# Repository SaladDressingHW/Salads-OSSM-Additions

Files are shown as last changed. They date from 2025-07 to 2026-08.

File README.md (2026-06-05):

This repository has all of my additions, mods and revamps open for Download.
If you like my work, consider supporting me on [Ko-Fi](https://ko-fi.com/deepfantasies)!
# Permissions
You are welcome to edit/alter/remix, print and use the provided files freely. You are also encouraged to make additions and share them should you see the need for them. You may redistribute only your edits/remixes/alterations and additions with credits to this repo at least. If you want to print my files to sell them, ask me for permission per message first. 

All of the above applies to every project here.
# Capstan OSSM XL
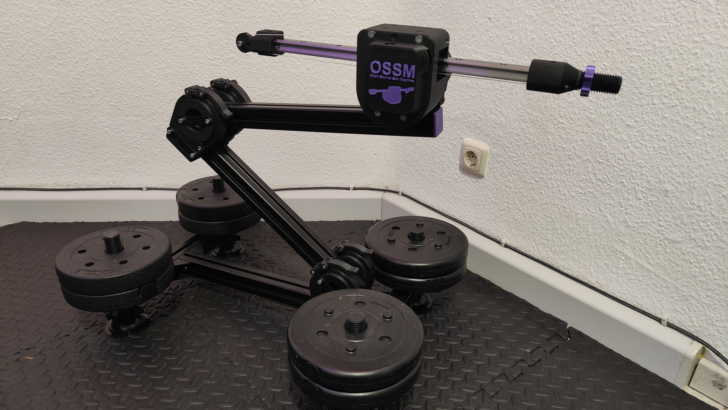
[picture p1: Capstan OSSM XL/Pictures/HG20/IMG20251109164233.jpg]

Revamp of the OSSM drive mechanism to use a capstan based version, enabling higher load use with a more powerful motor, namely the 60AIM40F.

Thread MGN12H: https://discord.com/channels/559409652425687041/1395456804464623817
Thread HG20: https://discord.com/channels/559409652425687041/1437149434143182959

# Capstan Proof of Concept
This was my first version. It is a proof of concept with quite a few flaws that I have abandoned to see if it is at all a viable concept. This is using 57AIM30 or 42AIM30 motors. You can try this first if you are sceptical to drop over a hundred bucks on a new motor. Bear in mind that quite a bit has changed since then. Changes that are not updated for this Proof of Concept. It worked good enough for me to use it, but it may not for you. The imo truly fleshed out Version is the Capstan XL.

Thread: https://discord.com/channels/559409652425687041/1331948206061256739

# 60AIM40F Motor Cover
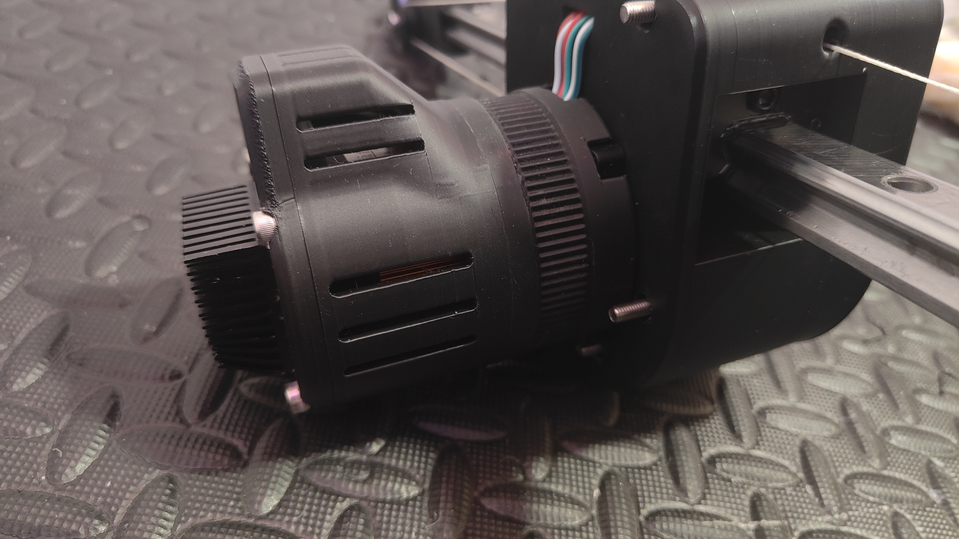
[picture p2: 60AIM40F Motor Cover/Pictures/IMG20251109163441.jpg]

Motor Cover for the 60AIM40F cover. Recommedned to only use with a heatsink attached to the back of the motor, where it gets really hot. Connects to armpits experimental 60AIM40F motor ring. For this, you need to replace the Nuts in the motor ring with M5x20 Coupling nuts. Then screw the Cover onto the motor with 4x M5x45 Hex Caps.

Thread: https://discord.com/channels/559409652425687041/1437144846510063636

# Double Penetration Attachment
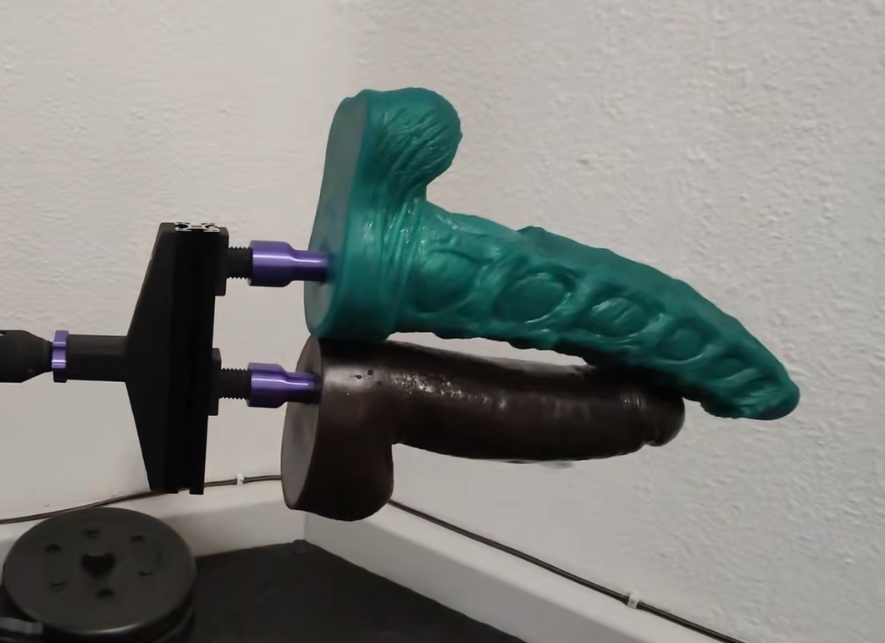
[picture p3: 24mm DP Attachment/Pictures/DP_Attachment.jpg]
DP_Attachment

A DP Attachment for 24mm threading. Uses a 200mm 3030 Aluminium Extrusion for extra stability and two on t-nuts slidable 24mm threads. Very heavy duty, very sturdy. Recommended to use with Capstan XL HG20 version but of course not required. Hardware needed are 4x M5x10 Hex Caps for the threads, 4x M5x20 for connecting the main part to the 3030 and 8 M5 T-Nuts.

Thread: https://discord.com/channels/559409652425687041/1437143419607847083

# Quick Change Strap Toy Mount remix

For compatibility with smaller print beds, I remixed @arctan and @marc_o_v [Quick Change Strap Toy Mount](https://discord.com/channels/559409652425687041/1278049440787337226). It detaches the straps from the Ring. From my experience, this is very secure and only slips under high load when lube come into contact with the connection. You need TPU filament.

Thread: https://discord.com/channels/559409652425687041/1279814763257397298

# Suction Cup Bracket

A bracket to mount [these](https://de.aliexpress.com/item/1005006355052746.html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) suction cups to 4040 extrusion (tested with aluxprofile Type I). The suction Cups are very strong, I use a total of 4 on my shicks mount. This has the big advantage to not loose any stability that comes with the shicks mount whatsover.
Requires one suction cup and one UNC-1/4 20 5/8" screw for each bracket.

Thread: https://discord.com/channels/559409652425687041/1395419104231559361

# Weight Plate Bracket

This is a bracket to mount standard 28-30mm inner diameter weight plates onto any extrusion. 2x M5x12 screws + 2x M5 T-Nuts required per Bracket 

Thread: https://discord.com/channels/559409652425687041/1279819188390596669

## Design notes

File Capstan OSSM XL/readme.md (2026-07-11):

Hundreds of hours of work as well as a lot of monetary resources go into this project! If you like my work, consider supporting me on [Ko-Fi](https://ko-fi.com/deepfantasies)!

# Capstan OSSM XL

Revamp of the OSSM drive mechanism to use a capstan based version, enabling higher load use with a more powerful motor, namely the 60AIM40F.

A Capstan Drive is based on rope and a pulley. For a nice video explaining the mechanism, check this awesome video by Aaed Musa: [https://www.youtube.com/watch?v=MwIBTbumd1Q](https://www.youtube.com/watch?v=MwIBTbumd1Q "https://www.youtube.com/watch?v=MwIBTbumd1Q")

**Why Capstan?**

The belt driven Version has shown for myself and quite a few others limitations. At higher torques, it would sometimes slip. Bear in mind, it could be that is the result from build or other errors.

**Comparison to the standard OSSM**

Pro:

 - same form factor
 - as quiet or quieter
 - 16.5cm rail length loss (e.g. 450mm rail -> 28.5cm stroke)
 - 2.7 times stronger (32kg compared to 12kg)
 - same speed
 - no slipping, reliable operation
 - PitClamp compatible
 - compatible with all custom end effectors

Con:

 - harder to build
 - bigger motor -> more expensive (~110€ shipped incl. tax to germany)
 - more to print
 - in extreme use cases there may be slipping of the rail over time, is fixed by rerunning homing
 - rope must always be tight -> regular checking
 - more heavy duty mounting recommended
 
The current iteration of the machine, that being the HG20 version, has been tested by me for many months now and has served all my needs. It also has been built and praised by many people in the KinkyMakers Discord Community.

Thread MGN12H: https://discord.com/channels/559409652425687041/1395456804464623817
Thread HG20: https://discord.com/channels/559409652425687041/1437149434143182959
# MGN12H vs HG20

**The MGN12H version is deprecated**

MGN12H rails and carriages get to their limit with 30cm+ cantilevers combined with heavy toys ~1.5kg and up. This results in louder operation, damaging of the bearings over time and deflection issues. So I recommend going with the HG20 Version if you plan to use big, heavy toys.
Additionally, the HG Version comes with a number of improvements such as a bigger drum and better rope guiding for even smoother operation.

I do consider the MGN12H version to be outdated so I do recommend going with HG20 if you can afford the +~40€ in cost.

# Rail Lengths
The Capstan Drum on the HG20 version was tested for 450mm. Shorter is always possible. 500mm and 550mm should be possible as well, but hasn't been tested by me (yet). Longer I do not recommend.

As for MGN12H, stay at 500mm or below.

# Rope
Use the rope I list (Liros DC pro 161). If you can't, try to source another dyneema dm20, sk99, sk75 max. diameter 1mm rope.

**DO NOT** use generic uhwmpe from aliexpress. Experiments from kind @neos have shown that the quality is shit. It stretches and breaks with load. It is essential that the rope stretches as little as possible. Lots of research has been done to find the correct rope. Stick to it. Or deviate at your own risk and cost.

# Printing
I have included .3mf file with configured settings. They require decent bridging performance. Some files don't have .3mf files. Those are quite straight forward to print. I always recommend 6 walls 20% infill.
# BOM
see /3D printed parts/MGN12H or /3D printed parts/HG20 respecively

Finally, special thanks to everyone that helped me and gave suggestions when I hit a wall!

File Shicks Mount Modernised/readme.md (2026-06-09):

# Shick's Mount Modernised
This is a modernisation, remix and compilation of the original Shick's Double Extrusion Mount as well as some mods done by [armpitMFG](https://github.com/armpitMFG). In addition to that, this is a centralized documentation for a heavy duty friendly mount, where even the biggest toys at long levers aren't able to make the mount slip. 

This is a WIP that is also still in testing, which is on hold due to lack of funds. Since it is just a reiteration (mostly making things bigger and stronger) of proven designs however, I am confident it will work nicely. I also have one more trick up my sleeve should the current strength still not suffice.

The Parts compiled and remixed here are the following:
| Part | Link | Modification(s) done |
|:---:|---|---|
| Original Double Extrusion Shicks mount | not hosted anywhere anymore, afaik | Just using the hinge long part + f3d files |
| 300° Hinge Plate by armpit | [Discord](https://discord.com/channels/559409652425687041/1214771415430078525) | Holes realligned, changed thickness |
| Lever Clamp System by armpit | [Discord](https://discord.com/channels/559409652425687041/1209004178421055598) | Reworked from the ground up to make it much bigger and more stable |
| Metal Hinge by Thomas & Me | [Discord](https://discord.com/channels/559409652425687041/1445780533991833810) | New Part |

# BOM
This BOM has heavy duty use in mind. Feel free to downscale for less demanding setups. More info in my beginners OSSM guide (releasing soon).
| Part | Amount | Link |
|:---:|---|---|
| 4040 Extrusion I recommend aluxprofile for people in Europe, Hinge is optimized for it (it's what I have on hand) | I use 2 x 400 mm for feet, 3 x 475 mm for arms | https://www.aluxprofil.de/aluminium-nutprofil-4040/a3619?m=4259 |
| 4040 end caps, or print your own | 8 for double arm | e.g. https://www.aluxprofil.de/profilabdeckkappe-4040/a3528 |
| 4080 corner brackets, best for heavy duty stability | 4 | https://de.aliexpress.com/item/1005009745995530.html |
| M8x80 adjustable lever | 1 per hinge | https://de.aliexpress.com/item/1005008368566274.html |
| Laser Cut Hinge Plates, stainless steel | 2 bottom (5mm) + 2 top (3mm) | "SideHingeLasered" files, order at your favorite laser cut shop, I use JLCCNC <br> [How to order from JLCCNC](https://github.com/SaladDressingHW/Salads-OSSM-Additions/blob/main/Salad's%20Beginner%20Guide%20to%20the%20'Ultimate'%20OSSM!/JLCCNC.md) |
| Hardware | see Hardware.txt | see Hardware.txt |

You will also need something to drill through the aluminium extrusion. A hand drill with according metal drill bit should suffice.

# Printing
**HingeLong**: You need 2 of these per Hinge. For 5mm hinge plates you will need the "Bottom" one, and for 3mm hinge plates the "Top" one. print them at an angle for best stability, see my .3mf. .3mf is for the Aluxprofile version as that is what I have. F3d file is attached so you can modify it to fit your own 4040 profile. Supports are needed. 6 Walls, 20% infill suffices.

**WasherBack**: Print one per hinge, again "Top" and "Bottom" versions depending on your plate thickness. Also needs to be printed at an angle, or it **will** break when tightening a lot. Again, see .3mf for orientation. Supports recommended. Print at 9 Walls or more to properly support the nut.

**WasherFront**: One is need per hinge. Print it 100% solid.

**TPU_Washer**: 2 per hinge are needed. Print it 100% solid. Out of TPU, as the name implies. I recommend printing TPU by Object for the least stringing. Especially if you haven't dried your Tpu like me.

# Assembly Guide
[Link](Assembly.md) (WIP)

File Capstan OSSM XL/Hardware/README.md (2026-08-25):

# BOM HG20

| Part | Cost (incl. shipping & tax) | link |
|---|---|---|
| 60AIM40F (+485 single turn version) | ~110€ | https://www.superbuy.com/en/page/buy/?url=https://item.taobao.com/item.htm?id=668578585661 <br><br> [How to order from Superbuy](https://github.com/SaladDressingHW/Salads-OSSM-Additions/blob/main/Salad's%20Beginner%20Guide%20to%20the%20'Ultimate'%20OSSM!/Superbuy.md) |
| RS485 to USB cable (for motor programming) | ~0€ | comes included with motor when bought from link above |
| OSSM Control Board + Remote (can buy board only if you want wireless remote) | 91 USD (excl. tax & shipping) | https://www.researchanddesire.com/products/ossm-reference-board |
| 2x 6 x 29.3 x 8 mm [id x od x w] U-Groove Pulley | ~8€ | https://de.aliexpress.com/item/1005007465275570.html |
| Hardware | ~30€ | see hardware/Hardware.txt |
| 1kg PLA | ~10€\kg | https://de.aliexpress.com/item/1005006639640810.html |
| 5m Liros DC pro 161 rope (or similar) | ~15€ | WW shipping: https://www.kitelineshop.com/ligne-liros-dcpro161-au-metre-c2x38222201  <br> US: https://www.mapleleafropes.com/store/category/new-england-ropes-hts-99-1 <br> Germany: https://www.blackbox-sailing.de/products/liros-dc-pro-kiteleine <br> EU: https://workshop.boardway.org/Liros-DC-Pro-161_1 |
| Bushing 20x24x40 (id x od x l) | ~5€ | https://de.aliexpress.com/item/1005009236377507.html |
| HG20 Linear Rail + HGH20HA Carriage | ~50€ (depending on length) | HG20 400/500mm + Carriage: https://de.aliexpress.com/item/4001272098866.html <br> HG20 other lengths: https://de.aliexpress.com/item/1005007417885303.html|
| Epoxy glue | ~3€ | https://de.aliexpress.com/item/1005007115129874.html |
| 4 pin JST PH2.0 header cable 30cm or solder/make your own | ~2€ | https://de.aliexpress.com/item/1005009087160808.html |
| 2 pin awg 18 or thicker 30cm | ~2€ | https://de.aliexpress.com/item/1005006614755156.html |
| 24mm id shrink tube | ~3€ | https://de.aliexpress.com/item/4000211463126.html |
| 36V 5+A power supply: Mean Well GST220A36-R7B + r7bf-p1j adaptor | ~68€ | GER: https://www.voelkner.de/products/2995507/MW-Mean-Well-GST220A36-R7B-Tischnetzteil-Festspannung-36-V-DC-6.1A-219.6W.html <br>**+**<br> https://www.voelkner.de/products/6716585/MW-Mean-Well-DC-PLUG-R7BF-P1J-Adapter.html <br> Look for your local distributors here: https://www.meanwell.com/distributors.aspx <br><br> Farnell, TME, Digikey and Rs-online ship to almost everywhere in the world! |
| **Total** | **~380€** | |

# BOM MGN12H [deprecated]

| Part | Cost (incl. shipping & tax) | link |
|---|---|---|
| 60AIM40F | ~110€ | https://www.superbuy.com/en/page/buy/?url=https://item.taobao.com/item.htm?id=668578585661 |
| OSSM Control Board + Remote (can buy board only if you want wireless remote) | 91 USD (excl. tax & shipping) | www.researchanddesire.com/products/ossm-reference-board |
| 5x MR115 bearings | ~3€ | https://de.aliexpress.com/item/1005007175995775.html |
| Hardware | ~30€ | see hardware/Hardware.txt |
| 1kg PLA | ~8€\kg | https://de.aliexpress.com/item/1005006639640810.html |
| 5m Liros DC pro 161 rope (or similar), ww shipping | ~15€ | https://www.kitelineshop.com/ligne-liros-dcpro161-au-metre-c2x38222201 |
| Bushing 20x23x30 (id x od x l) | ~5€ | https://www.agrolager.de/product_info.php?products_id=91534519 |
| MGN12H Linear Rail + Wagon | ~10-15€ (depending on length) | 450mm: https://de.aliexpress.com/item/1000007480470.html |
| Epoxy glue | ~3€ | https://de.aliexpress.com/item/1005007115129874.html |
| 4 pin JST header cable | ~2€ | https://de.aliexpress.com/item/1005007389108799.html |
| 2 pin awg 18 or thicker 30cm | ~2€ | https://de.aliexpress.com/item/1005006614755156.html |
| Kinesio Tape | ~3€ | buy locally (e.g. drug store) |
| 36V 5+A power supply (GST220A36-R7B + r7bf-p1j adapter) | ~68€ | https://www.voelkner.de/products/2995507/MW-Mean-Well-GST220A36-R7B-Tischnetzteil-Festspannung-36-V-DC-6.1A-219.6W.html <br>**+**<br> https://www.voelkner.de/products/6716585/MW-Mean-Well-DC-PLUG-R7BF-P1J-Adapter.html |
| **Total** | **~345€** | |

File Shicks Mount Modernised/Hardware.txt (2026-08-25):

- 16x M8x14 ISO7380 for 4x corner brackets
- 16x Sliding T-Nuts M8 for 4x corner brackets, check that it fits your extrusion! For Aluxprofile, take 3030 version: https://de.aliexpress.com/item/1005004658668930.html
- 6x M8x14 ISO7380 per Hinge
- 1x M8x60 Hex Cap per Hinge
- 3x M8x24 washer per Hinge
- 1x M8x40 washer per Hinge https://de.aliexpress.com/item/1005002399622506.html
- 6x sliding T-Nuts M8 per Hinge
- 2x M8 Nuts per Hinge

optional for GST220A36 power supply:
- 2x M5x20 Hex Cap
- 2x M8x20 Hex Cap
- 2x M5 Nut
- 2x M8 sliding T-Nut

Hex Cap: My designs are made for DIN 912/ISO 4762 Norm

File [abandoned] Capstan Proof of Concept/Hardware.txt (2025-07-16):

Hardware:

Tensioner:
 2x M3x30 Hex Cap
 4x M5x25 Hex Cap
 1x M5x50 Hex Cap
 
 2x M3 Nut
 5x M5 Nut

Motor Head:
 42AIM:
  2x M3x12 Countersunk
  6x M3x12 Hex Cap
  1x M4x16 Hex Cap
  5x M5x35 Countersunk

  5x M5 Nut
 
 57AIM30:
  1x M4x16 Hex Cap
  4x M5x30 Hex Cap
  2x M5x50 Hex Cap
  2x M5x80 Hex Cap
  
  4x M5 Nut

End Effector:
 2x M3x16 ISO7380
 2x M3 Nuts

Rope:
any of dyneema dm20, sk99, sk75 max 1mm diameter is a good option
I recommend, and the pulley is modeled for: liros dc pro 161 (sk99)
ww shipping shop: https://www.kitelineshop.com/ligne-liros-dcpro161-au-metre-c2x38222201

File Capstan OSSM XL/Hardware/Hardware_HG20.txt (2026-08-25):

2x M3x12 Hex Cap
4x M4x16 ISO7380
2x M5x45 Countersunk
4x M5x80 Countersunk
2x M6x25 Countersunk
4x M5x20 Hex Cap
3x M5x30 Hex Cap
4x M5x65 Hex Cap
1x M5x110 Hex Cap Fully threaded https://de.aliexpress.com/item/1005005879037174.html
11x M5 Nuts
4x M4 Nuts
2x M3 Nuts

Motor Cover:
4x M5x65 Hex Cap
4x M5x20 Coupling Nuts

Hex Cap: My Designs are made for DIN 912/ISO 4762 Norm

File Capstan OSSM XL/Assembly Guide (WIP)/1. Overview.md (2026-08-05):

# Welcome!
So you have decided on building a Capstan OSSM XL, or at least are thinking about it! It's always good to take a look before starting the process as well, so good on you! This doc is the first part of the Assembly Guide, and gives an Overview of the process. So let's get started!

<br>

## Step 1: Sourcing parts
This is probably the most unattractive part. This build has a lot of parts that you need. There are two ways that you can go about that!

#### The easy route:
 Head over to my [Etsy](https://www.etsy.com/shop/SaladsSexMachines) and order a Hardware Kit! Every item that you need to buy (except tools) is included there. Some items like the recommended rope can be hard to source in some parts of the world, so this might be a good option for you

#### The DIY route:
 Head over to the [BOM](https://github.com/SaladDressingHW/Salads-OSSM-Additions/tree/main/Capstan%20OSSM%20XL/Hardware) and source everything yourself! Quite a few things you will have to look for locally. More info in the following doc, [`Tools And Parts.md`](./2.%20Tools%20And%20Parts.md).

<br>

## Step 2: Print your parts
Again, you can do this two ways!

#### Printed Parts Kit:
3D printed part kits are ready to purchase, again from my [Etsy](https://www.etsy.com/shop/SaladsSexMachines). You can also message me to ask about personalizion options!

#### Print it yourself:
Head over to the [directory with the 3d printed parts](https://github.com/SaladDressingHW/Salads-OSSM-Additions/tree/main/Capstan%20OSSM%20XL/Hardware/3D%20printed%20parts/HG20). There are .stl and .3mf files both. The .3mf files include the settings and print orientations I use, and in some cases also painted supports. There are also .step files for all parts and in some cases .f3d as well so you can edit parts in case you want/need to modify something. More infos are provided in the following document, [`Tools And Parts.md`](./2.%20Tools%20And%20Parts.md). 
**Warning:** This project is **not** beginners friendly to print. You are expected to have some experience with 3D printing and a solid understanding of print settings and print optimization!

<br>

## Step 3: Prerequisites
There are still some other things that need to be done before assembly. Namely programming your Motor, flashing your PCB and glueing your Capstan Drum. Details and tutorials on how to do that are in the third document, [`Prerequisistes.md`](./3.%20Prerequisites.md).

<br>

## Step 4: Assembly
With everything sourced, printed and prepared, the machine can finally get assembled! This process is documented in the fourth and final document, [`Assembly.md`](./4.%20Assembly.md).

<br>

## Accessories and Mounting
You might be wondering what else you need. This guide is **only** for the Capstan OSSM XL, without any accessories or mounting. If you want or need guidance on the whole ecosystem, including mounting, modding and accessory options, check out my [Beginner's Guide](../../Beginner's%20Guide%20to%20the%20'Ultimate'%20OSSM!/)!

<br>

## Community
Finally, if you have any questions, problems, concerns, feedback or you just want to chat and share your OSSM (awesome) project, head over to the [Kinky makers Community over on discord](https://discord.gg/KVAGhvUkw)! We are a healthy community full of kinky makers and diyers happy to welcome anyone who is interested in it!

Happy building!

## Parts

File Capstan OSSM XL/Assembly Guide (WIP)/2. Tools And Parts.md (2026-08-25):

# Tools and Parts
This document gives and overview off all the parts, Hardware and Tools you need.

## 3D Printed Parts
These parts all need to be printed once! The files can be found [here](/../Hardware/3D%20printed%20parts/HG20/), both.stl and .3mf.
#### Print Settings:
Generally, the .3mf files contain the settings I print with, which are my recommended settings. However, each printer setup, print profiles and material is different, so please check and adjust settings and profiles accordingly. The .3mf files are optimized for eSun PLA Basic. In the following there are the core guidelines on what to pay attention to!
1. **Orientation:** Ignore the .stl orientations. Refer to the .3mf orientations instead. Do not reinvent the wheel. The orientations are crucial for the designs strength. The parts **will** break in the wrong orientation.
2. **Strength:** Most parts should be printed with at least 6 walls and 20% gyroid/cubic/similar infill. Adjust as needed depending on what material you print. Check the .3mf files to see which ones need less.
3. **Supports:** Due to the complexity of the design, many parts need supports. Please refer to the .3mf files for recommended support stucture. Some .3mf files have painted supports as well, for optimal printing.
4. **Layer Height:** Basically all prints are made for 0.2mm layer height and print well with it. The End Effector benefits strongly form adjsuting to 0.12mm or even 0.8mm layer height for a higher quality thread and overhangs. Many parts also benefit from variable layer height. Again, see the .3mf files to see if it is recommended on a part.
5. **Nozzle Size:** I have only ever printed with a 0.4mm nozzle, and therefore all my prints work well with that!
### Capstan Drum 
| Preview | File | Preview | File |
|---|---|---|---|
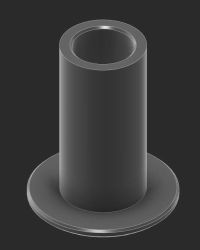
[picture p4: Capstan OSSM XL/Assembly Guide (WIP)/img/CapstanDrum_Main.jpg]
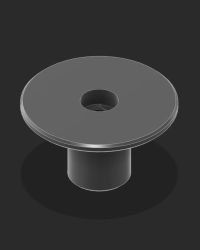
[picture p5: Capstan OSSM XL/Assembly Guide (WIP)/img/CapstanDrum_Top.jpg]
|  | `CapstanDrum_Main.stl` |  | `CapstanDrum_Top.stl` |

### Motor Head
| Preview | File | Preview | File |
|---|---|---|---|
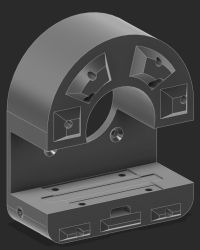
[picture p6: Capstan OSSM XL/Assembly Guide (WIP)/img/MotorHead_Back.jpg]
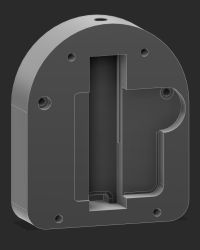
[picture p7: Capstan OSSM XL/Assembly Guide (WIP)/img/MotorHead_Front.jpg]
|  | `MotorHead_Back.stl` |  | `MotorHead_Front.stl` |
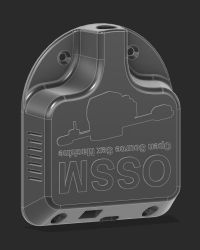
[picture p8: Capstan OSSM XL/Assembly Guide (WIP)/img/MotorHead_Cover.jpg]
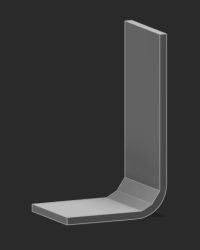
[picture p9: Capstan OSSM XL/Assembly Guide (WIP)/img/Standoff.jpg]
|  | `MotorHead_Cover.stl` |  | `Standoff.stl` |
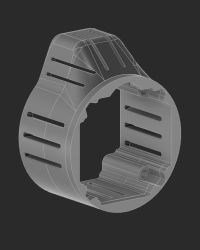
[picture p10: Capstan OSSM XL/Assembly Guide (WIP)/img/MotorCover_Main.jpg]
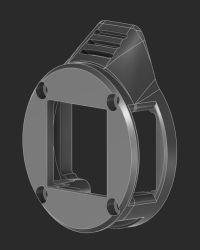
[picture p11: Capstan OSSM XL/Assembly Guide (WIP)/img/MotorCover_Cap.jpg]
|  | `MotorCover_Main.stl` |  | `MotorHead_Front.stl` |
|  | `Pitclamp_MotorRing_60AIM40F.stl` |  |  |

### EndEffector
| Preview | File | Preview | File |
|---|---|---|---|
|  | `EndEffector_<Hole End Offset>mm.stl` |  | `EndEffector_PulleyCover.stl` |

### Rail End
| Preview | File | Preview | File |
|---|---|---|---|
|  | `RailEnd_<Hole End Offset>mm.stl` |  | `RailEnd_PulleyCover.stl` |

### Tensioner
| Preview | File | Preview | File |
|---|---|---|---|
|  | `Tensioner_Bottom.stl` |  | `Tensioner_Top.stl` |

<br>

## Bill of Materials
The sourcing is mainly done for Gemrany, where I am based. Many linked parts ship worldwide or within Europe as well. You will need to look for your own sources, for your region if the provided sources don't work for you. Prices are rough estimates, with EU VAT, but without any additional costs attached (like the stupid new 3€/category from china imports).

**Rope:** The rope listed below can be quite hard to get depending on your region. There is a shop that claims worldwide whipping on the rope I develop the machine for, but users have reported theird orders getting canceled. You can still try it, it's still listed. I do not have the time and ressources to try lots of different ropes for every region. You have two options:
   1. Ask someone to ship it to you (Forwarding)
   2. Source a rope yourself and test it yourself. The important part here is that the rope is made out of Dyneema. Best case is Dyneema DM20, but Sk99 and SK78 work great as well. The Liros DC Pro 161 is made out of Dyneema Sk99. **Do not buy cheap aliexpress UHWMPE**. Testing has found that it is absolute crap that creeps ands stretches by unholy amounts. The second important part is that it is around 1mm in diameter, and this is where things get a bit harder most of the time. I wouldn't recommend going over 1.1-1.3mm. Thicker diameters may take away too much space on the drum, but feel free to test yourself. And if you do, pelase report!

| Part | Cost (incl. shipping & tax) | Link |
|---|---|---|
| 60AIM40F (+485 single turn version) | ~110€ | https://www.superbuy.com/en/page/buy/?url=https://item.taobao.com/item.htm?id=668578585661 <br><br> [How to order from Superbuy](https://github.com/SaladDressingHW/Salads-OSSM-Additions/blob/main/Salad's%20Beginner%20Guide%20to%20the%20'Ultimate'%20OSSM!/Superbuy.md)|
| RS485 to USB cable (for motor programming) | ~0€ | comes included with motor when bought from link above |
| OSSM Control Board + Remote (can buy board only if you want wireless remote) | 91 USD (excl. tax & shipping) | https://www.researchanddesire.com/products/ossm-reference-board |
| 2x 6 x 29.3 x 8 mm [id x od x w] U-Groove Pulley | ~8€ | https://de.aliexpress.com/item/1005007465275570.html |
| Fasteners & Nuts | ~30€ | see section below |
| 1kg PLA | ~10€\kg | use whatever works for you |
| 10m Dyneema DM20/SK99/SK78 Rope <br> Standard: Liros DC Pro 161 <br> NA: New England Ropes HTS 99 | ~15€ | WW shipping: https://www.kitelineshop.com/ligne-liros-dcpro161-au-metre-c2x38222201  <br> US: https://www.mapleleafropes.com/store/category/new-england-ropes-hts-99-1 <br> Germany & EU: https://www.blackbox-sailing.de/products/liros-dc-pro-kiteleine <br> EU: https://workshop.boardway.org/Liros-DC-Pro-161_1 |
| Bushing 20x24x40 (id x od x l) | ~5€ | https://de.aliexpress.com/item/1005009236377507.html |
| HG20 Linear Rail + HGH20HA Carriage | ~40€ (depending on length) | HG20 400/500mm + Carriage: https://de.aliexpress.com/item/4001272098866.html <br> HG20 other lengths: https://de.aliexpress.com/item/1005007417885303.html |
| Epoxy glue | ~3€ | https://de.aliexpress.com/item/1005007115129874.html |
| 4 pin JST PH2.0 header cable 30cm | ~3€ | https://de.aliexpress.com/item/1005009087160808.html |
| 2 pin awg 18 or thicker 30cm | ~2€ | https://de.aliexpress.com/item/1005006614755156.html |
| 24mm id shrink tube | ~4€ | https://de.aliexpress.com/item/4000211463126.html |
| Heat Sink 40x40x20mm | ~7€ | https://de.aliexpress.com/item/1005007090772998.html |
| 36V 5+A power supply: Mean Well GST220A36-R7B + r7bf-p1j adaptor | ~68€ | GER: https://www.voelkner.de/products/2995507/MW-Mean-Well-GST220A36-R7B-Tischnetzteil-Festspannung-36-V-DC-6.1A-219.6W.html <br>**+**<br> https://www.voelkner.de/products/6716585/MW-Mean-Well-DC-PLUG-R7BF-P1J-Adapter.html <br> Look for your local distributors here: https://www.meanwell.com/distributors.aspx <br><br> Farnell, TME, Digikey and Rs-online ship to almost everywhere in the world! |
| Isopropyl Alcohol || local Hardware Store |
| **Total** | **~390€** | |

<br>

## Fasteners & Nuts
The table below lists all the dasteners and nuts you need and what it is used for.

| Screw  | Type | Amount | Usage |
|---|---|---|---|
| M4x16  | Button Head | 4 | Tensioner Rope Clamp |
| M5x45  | Countersunk | 2 | Attaching Motor Head Back to Motor |
| M5x80  | Countersunk | 4 | Attaching Motor Head Cover to Motor Head |
| M6x25  | Countersunk | 2 | Mounting U-Groove Pulley to End Effector and Rail End |
| M3x12  | Hex Cap | 2 | Attaching the PCB to the Motor Head Cover |
| M5x20  | Hex Cap | 4 | Mounting HGH20HA Carriage to Motor Head Back |
| M5x30  | Hex Cap | 3 | 2x: Mounting End Effector and Rail End to HG20 Rail <br> 1x: Securing Capstan Drum to Motor shaft |
| M5x65  | Hex Cap | 8 | 2x: Attaching Motor Head Back to Motor <br> 2x: Attaching Motor Head Front to Motor Head Back <br> 4x: Mounting Motor Cover to Motor Head |
| M5x110 | Hex Cap, [fully threaded](https://de.aliexpress.com/item/1005005879037174.html) | 1 | Rope Tensioner Screw |
| M3 | Nuts | 2 | Attaching the PCB to the Motor Head Cover |
| M4 | Nuts | 4 | Rope Tensioner Clamp |
| M5 | Nuts | 9 | 6x: Back of Motor Head Back <br> 2x: End Effector and Rail End <br> 1x: Rope Tensioner Clamp |
| M6 | Nuts | 2 | End Effector and Rail End |
| M5x20  | Coupling Nuts | 4 | Coupling Motor Head to Motor Cover |

#### Standards:
- Button Head Screws: ISO 7380
- Countersunk Screws: ISO 10642
- Hex Cap: ISO 4762, except fully threaded M5x110
- Nuts: DIN 934, ISO 4033 should work

## Tools
You don't need much at all to build this machine! Very basic tools:
1. Screwdriver
2. Hex Bits sizes 2.5mm, 3mm & 4mm. I use this bitset: https://de.aliexpress.com/item/1005006233315642.html
3. Slotted Bit 2mm
4. Pliers
5. lint free cloth (e.g. glasses cleaning cloth)
6. household single use gloves
7. Heatgun/Hairdryer/Lighter

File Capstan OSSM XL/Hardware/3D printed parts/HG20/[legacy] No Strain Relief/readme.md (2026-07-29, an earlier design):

### Only use this version if you do not have or can buy the recommended Power Supply, Mean Well GST220A36.R7B + Adapter. This version is now considered legacy. I strongly recommend making the version with integrated Strain Relief!
hardware is the same as the version with strain relief!

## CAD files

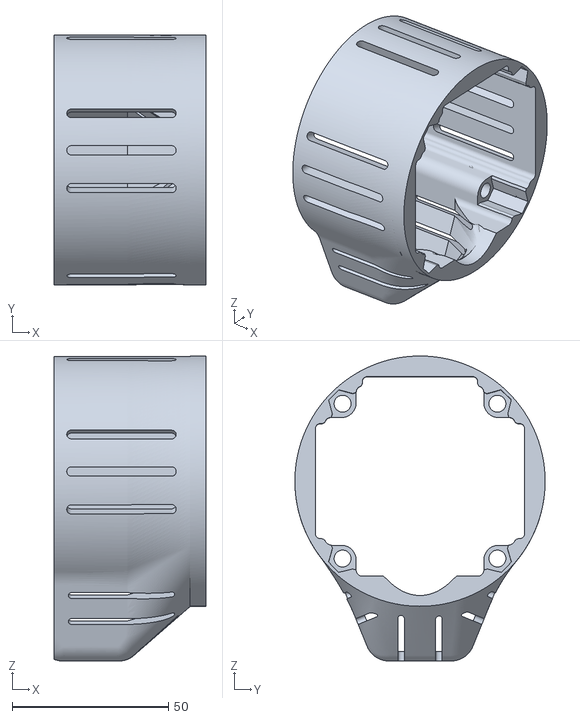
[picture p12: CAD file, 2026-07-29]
Capstan OSSM XL/Hardware/3D printed parts/HG20/MotorCover_Main.stl
48.4 x 80.0 x 97.5

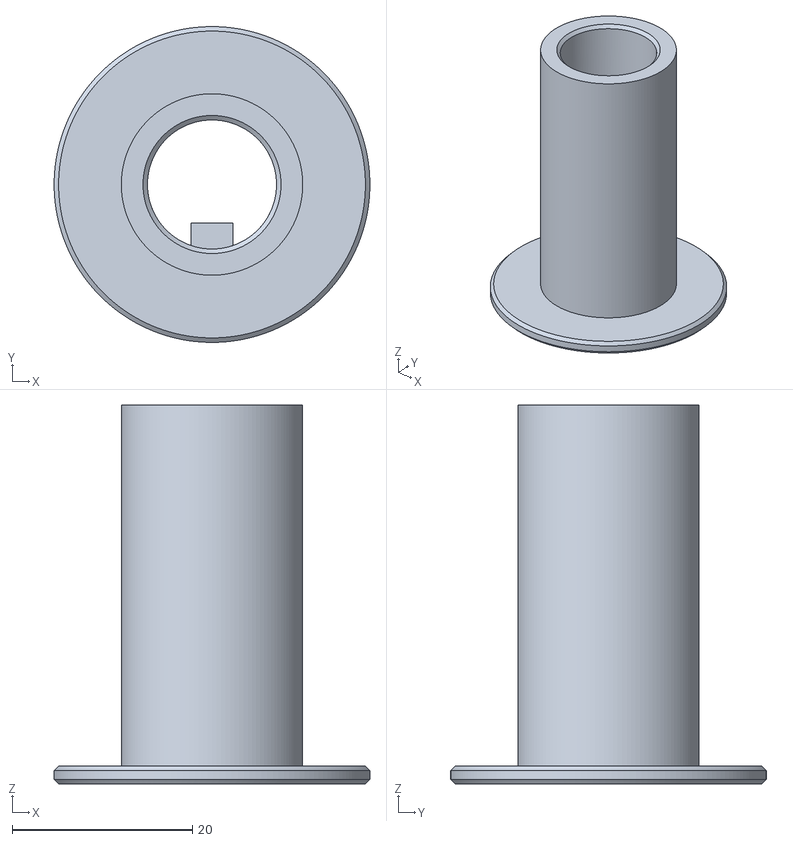
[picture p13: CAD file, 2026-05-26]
Capstan OSSM XL/Hardware/3D printed parts/HG20/CapstanDrum_Main.stl
35.0 x 35.0 x 42.0

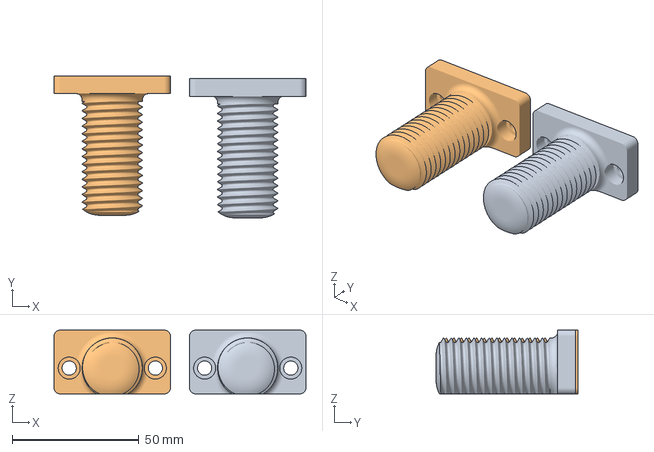
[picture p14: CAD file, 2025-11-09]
24mm DP Attachment/DP_Attachment_Thread.3mf
99.4 x 56.0 x 25.2 mm
DP_Attachment_Thread.stl x 2

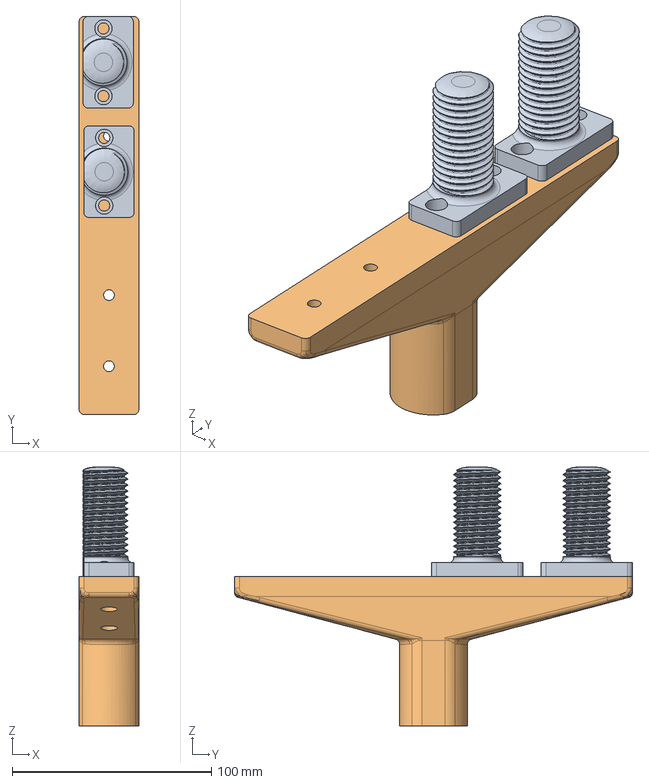
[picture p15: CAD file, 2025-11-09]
24mm DP Attachment/STEP/DP_Attachment.step
30.0 x 200.0 x 130.0 mm

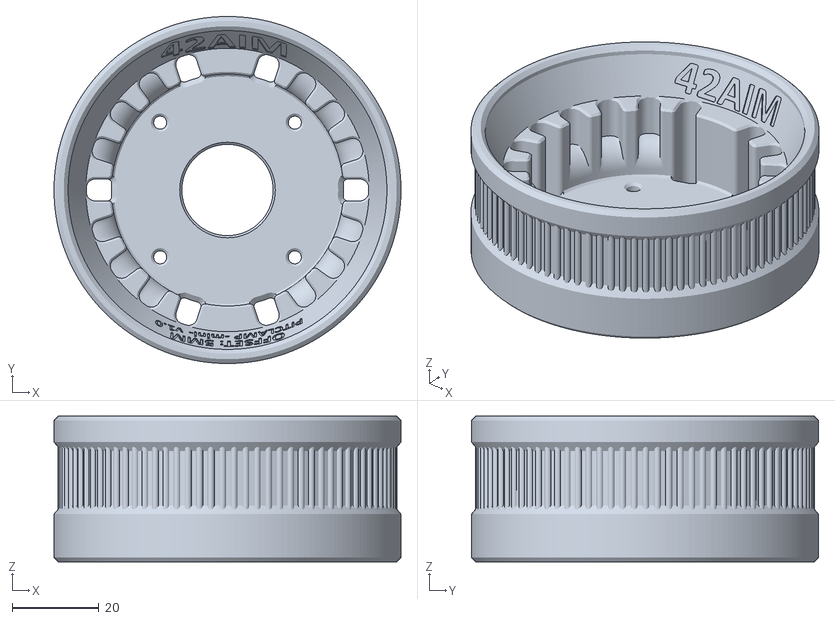
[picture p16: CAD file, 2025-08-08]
[abandoned] Capstan Proof of Concept/42AIM30/PitClamp Mini - Ring - 42AIM - Centered - 5mm Offset.stl
79.9 x 79.9 x 33.5

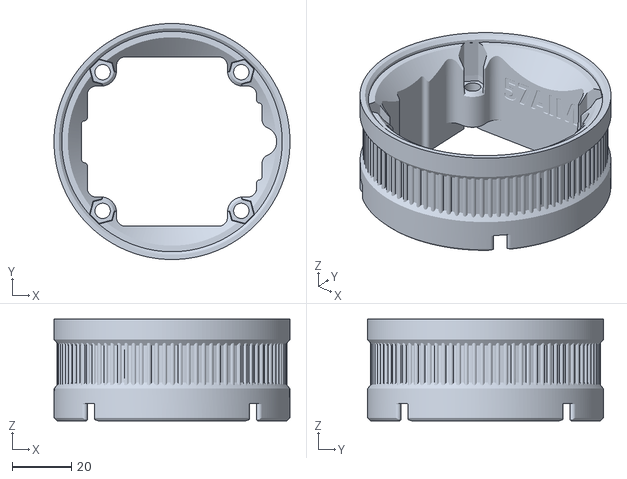
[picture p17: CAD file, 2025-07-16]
[abandoned] Capstan Proof of Concept/57AIM30/PitClamp Mini - Ring v1.1 - 57AIM - 5mm Offset +Passthru.stl
80.0 x 80.0 x 34.5

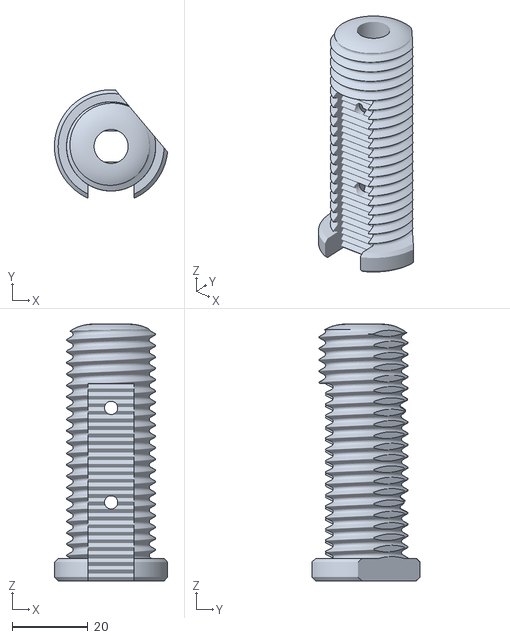
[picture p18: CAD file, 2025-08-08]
[abandoned] Capstan Proof of Concept/End Effector/End Effector.stl
29.9 x 28.7 x 68.0

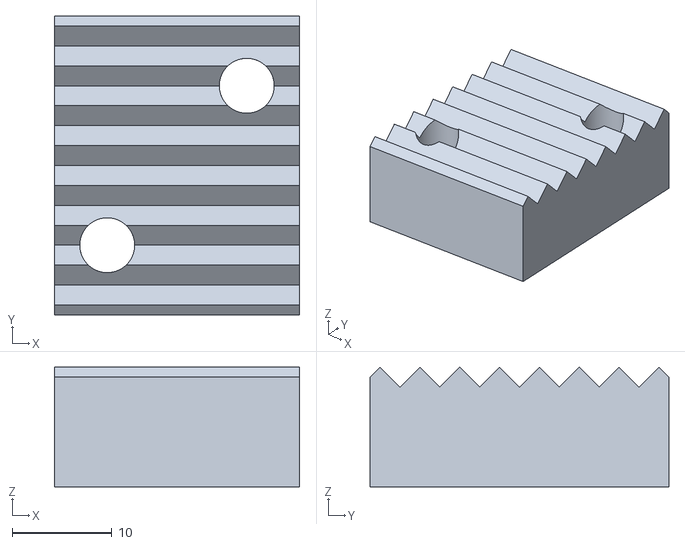
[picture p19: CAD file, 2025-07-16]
[abandoned] Capstan Proof of Concept/Tensioner/RopeClampUpper.stl
24.6 x 30.0 x 12.0

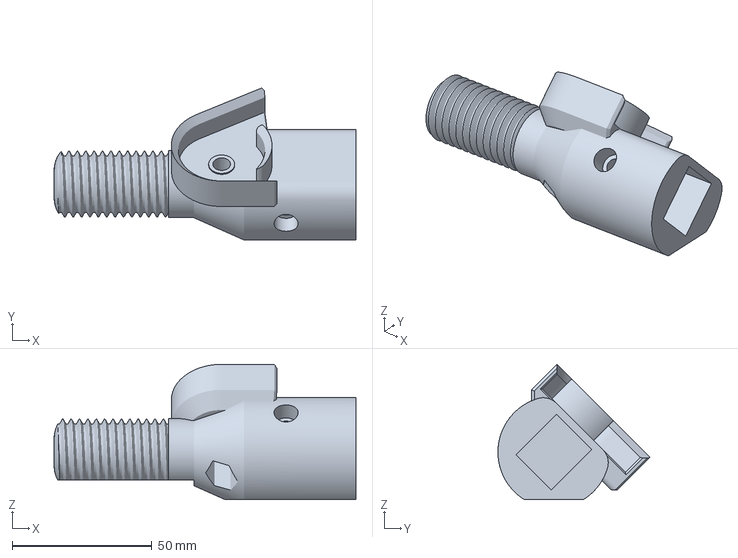
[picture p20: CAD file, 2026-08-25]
Capstan OSSM XL/Hardware/3D printed parts/HG20/EndEffector_15mm.3mf
108.0 x 54.4 x 48.4 mm

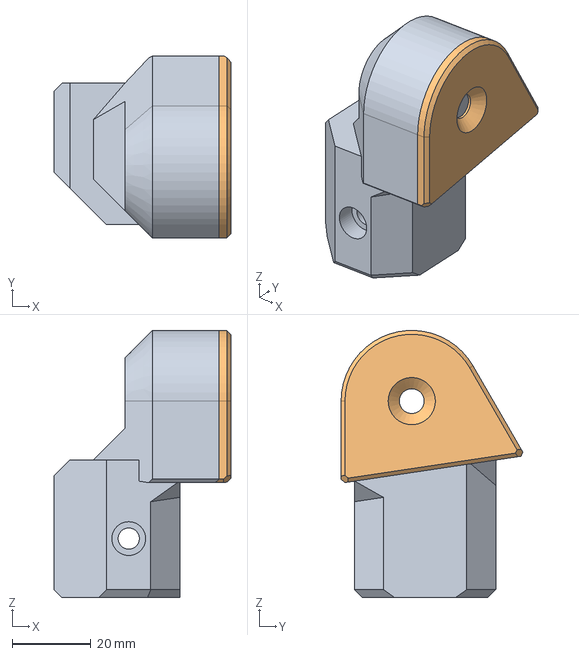
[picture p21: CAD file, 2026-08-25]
Capstan OSSM XL/Hardware/3D printed parts/HG20/STEP/RailEnd.step
45.0 x 46.3 x 68.0 mm

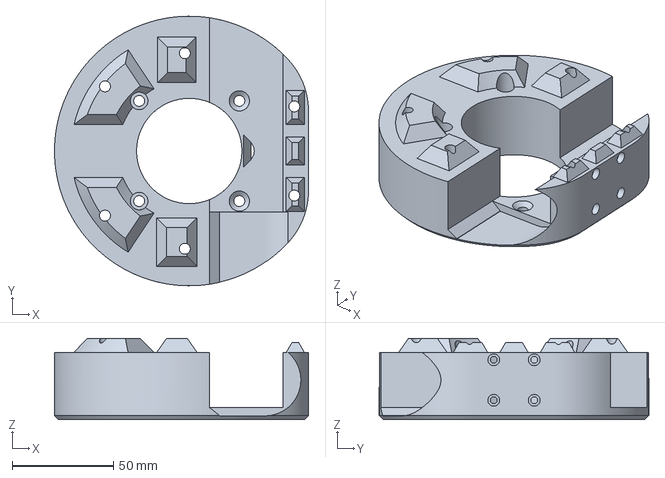
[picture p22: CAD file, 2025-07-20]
Capstan OSSM XL/Hardware/3D printed parts/MGN12H/AIO Mod/MotorHead_BackAIO.3mf
125.5 x 133.1 x 40.2 mm

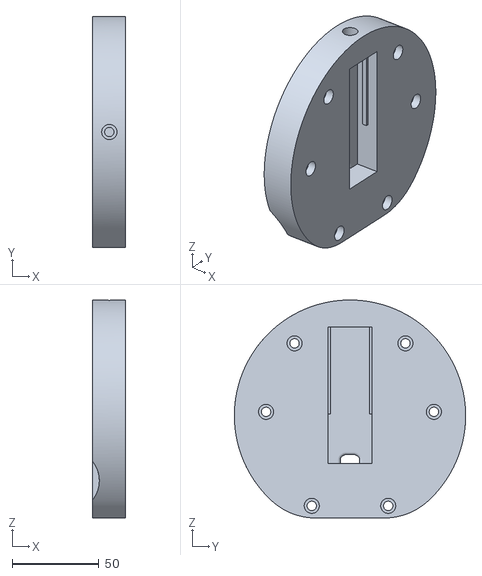
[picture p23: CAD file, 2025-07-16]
Capstan OSSM XL/Hardware/3D printed parts/MGN12H/Normal/MotorHeadFront.stl
19.1 x 133.1 x 125.5

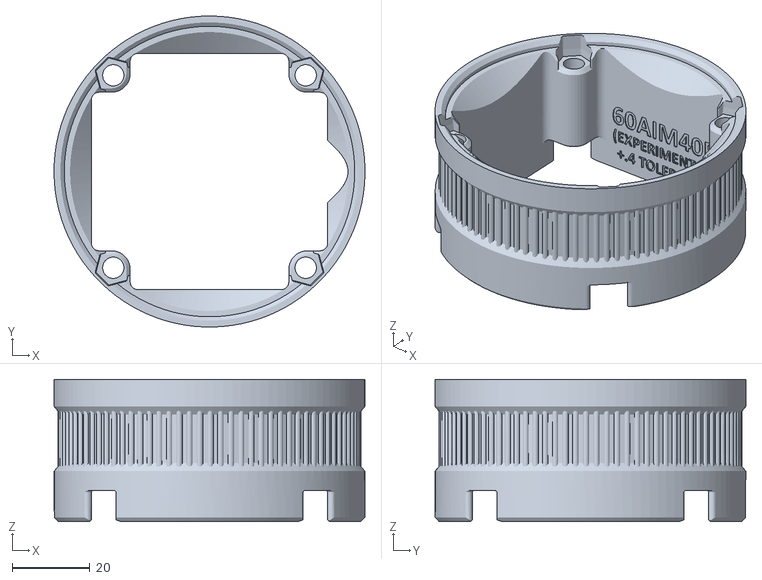
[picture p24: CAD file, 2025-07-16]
Capstan OSSM XL/Hardware/3D printed parts/MGN12H/PitClamp Mini - Ring - 60AIM40F - 7mm Offset + Bigger Passthru - by @armpit.stl
80.0 x 80.0 x 36.5

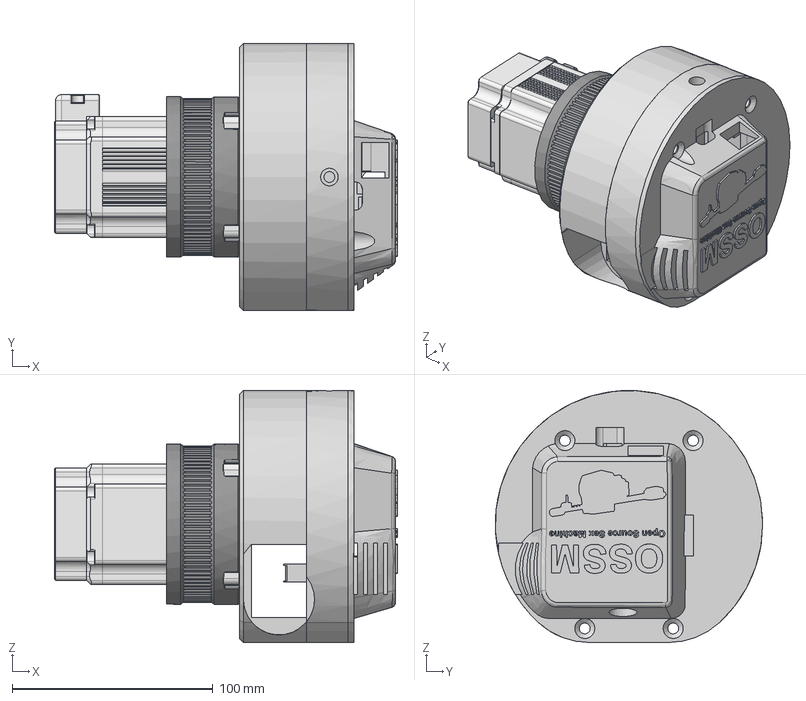
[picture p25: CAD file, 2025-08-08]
Capstan OSSM XL/Hardware/3D printed parts/MGN12H/STEP/MotorHead_60AIM40F.step
170.7 x 133.1 x 125.5 mm
6040方电机_简化_1
Graphic
60AIM40F Ring

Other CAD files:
Quick Change Strap Toy Mount Remix/Ring40mm.stl
Shicks Mount Modernised/SideHingeLasered_Bottom.step
Suction Cup Bracket/SuctionCupBracket - 3030 Amazon by neos.step
[abandoned] Capstan Proof of Concept/End Effector/End Effector Upper.stl
24mm DP Attachment/DP_Attachment.3mf
24mm DP Attachment/DP_Attachment.stl
24mm DP Attachment/DP_Attachment_Thread.stl
Capstan OSSM XL/Hardware/3D printed parts/HG20/CapstanDrum.3mf
Capstan OSSM XL/Hardware/3D printed parts/HG20/CapstanDrum_HGR.f3d
Capstan OSSM XL/Hardware/3D printed parts/HG20/CapstanDrum_Top.stl
Capstan OSSM XL/Hardware/3D printed parts/HG20/EndEffector_10mm.3mf
Capstan OSSM XL/Hardware/3D printed parts/HG20/EndEffector_10mm.stl
Capstan OSSM XL/Hardware/3D printed parts/HG20/EndEffector_15mm.stl
Capstan OSSM XL/Hardware/3D printed parts/HG20/EndEffector_20mm.3mf
Capstan OSSM XL/Hardware/3D printed parts/HG20/EndEffector_20mm.stl
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

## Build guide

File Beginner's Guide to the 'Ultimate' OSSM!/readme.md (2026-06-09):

**WIP**

# Welcome!
Are you **sick and tired** of **underwhelming** machines that are just copy pastes of each other? **Annoying** stroke depth adjustment by changing fly wheel radius? The same sinusoidal back and forth movement with **no pattern control**? **Underwhelming force** that **stalls** at anything bigger than a **toothpick**?
Ohhh do I have a solution for you! :DD

All tongue in cheek aside, that solution is called the **OSSM**, pronounced "awesome" and short for "Open Source Sex Machine"! As the name implies, it is an open souirce sex machine project, hosted on the official OSSM Github [here](https://github.com/KinkyMakers/OSSM-hardware/tree/main), with it's development and community based on the KinkyMakers Discord (I know, Discord for developing, bleh) [here](https://discord.gg/NcueGt87u).
The main features that sets it apart from other machines is real time adjustable stroke length and depth, pattern control with a big selection as well as documentation how to make your own, compactness, and strength. And all this at a relatively low price. It is 3d printed, and relatively easy and beginner friendly to assemble with great documentation. All other parts are of the shelf components you can easily get at places like aliexpress or amazon. Pick your poison :) I recommend checking out the repository for more information on the project.

## Do I need an alternative design?

Now while the machine is already quite powerful as is, with a pushing force of 12kgf (meaning it can push 12kg), it may not prove to be enough force for many users that, like myself, like to use **BIG** toys. From my and many other users experience, the standard build of the OSSM tends to stall with larger toys. Where that point is, is different from person to person. For some, it happens at sizes like large bad dragon toys, for others that is already the case with medium sized toys, especially knotted ones. That stalling is even more so the case for people with strong pelvic floors, especially if they cramp a lot during stimulation. This reasoning applies to both vaginal and anal use, although anal generally requires more force than vaginal use.

If you want to test out how much force you need, a hacky but simple way of doing that is taking the biggest toy that you want to use with it, place it on a scale and sit down on it. Put on all the force you can and try to push the toy out a bit for good measure. Add a few kg of redundancy to the biggest value you see on the scale, and you have your required force.
If that value is below 12kg, you are probably good to go with the standard design! But I do recommend to keep reading, there are a two other things to consider as well!

<br>

The first thing to consider is toy weight! The standard design uses a MGN12H linear rail. It's definitely a very great and capable rail that works for most toys, but the longer the rail length and therefor possible stroke depth, the higher the load will be on the bearing, that being the carriage block. This goes along with weight of toys. So, if you use bigger toys, that are also heavier and require longer stroke length to use the whole length on the machine, you multiply the load on the rail mounting. The force gets so high, that it can damage the rail over time and/or make it very loud.
So, the logical conclusion, at least mine, is to throw a bigger, beefier rail at it!

Now what you essentially need to check is the weight of your toys! The rail length you will choose does matter here, but as a general rule of thumb I recommend skipping on the standard design if you want to use toys heavier than 1.5kg!

<br>

The second thing that may influence your decision, is your expected "progress". Do you expect to size up over time? How much do you expect to size up? Will that push you over the edge where you might need a stronger machine? This is worth thinking a bit about, or you might have to upgrade at some point, which means you essentially spend the same money twice.

## So what is the alternative?
For the above described personal gripes I have with the standard design, I developed my own machine. That machine is called the **Capstan OSSM XL**, or **Capstan XL**. It completely revamps the Hardware to enable use of a motor ~twice as powerful as the original one, giving you a total of 32kgf pushing force! By this point it has been tried and tested by many users, and the feedback incorporated into multiple updates and iterations, to this day.

## What *exactly* is the Capstan XL?

For this question, I will kindly refer you to my readme over here: https://github.com/SaladDressingHW/Salads-OSSM-Additions/blob/main/Capstan%20OSSM%20XL/readme.md

## Do I need one?
Well that is for you to deecide of course! But in my opinion, if you fall out of the  (in my opinion) restrictions of the standard design, I don't see a reason to not go with the Capstan XL! If you do have any questions or are unsure, feel free to hop on the discord and ask away! other methods of getting in contact with me are gonna get established in the future!

## Okay I have decided!
Great! If you have decided for the standard build, just head over to the main repo and follow the instructions there!
If you have decided for the Capstan XL instead, you have multiple options>
   1. DIY all the way! <br>
    The [Capstan XL repository](https://github.com/SaladDressingHW/Salads-OSSM-Additions/tree/main/Capstan%20OSSM%20XL) has clear instructions on how you can build your own machine! Start by reading through it, take a look at the readme, BOM and Assembly instructions! Bear in mind that this is definitely not the best project for beginners! The 3D prints are more difficult and the assembly is definitely more involved and difficult than the standard build. That being said, I put a lot of effort in making it as accessible as possible with the time I have on my hands!
   2. Assemble yourself Kits <br>
    If you don't want to go through the pain (do some people actually like it?) of sourcing aaall the different parts, 3D printing every part and making sure everything fits as well 3D printing everything yourself, you can get DIY kits in different variations on my Etsy page! This also supports me and the continuous development of the machine!
   3. Buy assembled! <br>
      If you don't want to bother with neither sourcing nor a bit finicky assembly, you can buy assembled Capstan XL on the same Etsy page. As with the option before, this als odirectly supports me and the development of this and other projects!

Bear in mind that my Etsy currently only serves continental Europe!

## What else do I need?
There are quite a lot more things you need for a fully functioning machine. Because that is so much, I have divided this guide up into multiple parts. Click on the links below to get to the documents. This also serves as an overview.

1. **Mounting**:<br>You need to attach the machine somehow to something that makes it able to hold the machine in place, whereever you want. For this, there are quite a few Mounting options. See more in the dedicated file.
2. **Toy Attachments**:<br> No matter the version, the OSSM comes with a 24mm thread at the front, the so called "End Effector". This is a universal standard where all different Mounting and attachment systems for toys get screwed onto!
3. **Remote**:<br> Well, you need something to actually control the machine, right?
4. **Accessories**:<br> More optional parts that can be nice to have, depending on your preferences and use case!

## That's it!
This and the documents linked above should give you an guide you through everything you need! Bear in mind that I am not able to cover everything, because there is jsut too much! Additionally, there is new stuff being released quite regularily. So if you are not quite happy with what I list, always feel free to hop onto the discord and check out all the amazing stuff in #ossm-print-testing and #member-projects!

And last but not least: 

**Have fun!**

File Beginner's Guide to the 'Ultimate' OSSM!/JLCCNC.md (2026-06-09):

This short guide covers on how to order laser cut designs at JLCCNC, e.g. for the hinge for the [Shick's Mount Modernised]()!
1. Go to [JLCCNC's Website](https://jlccnc.com/)
2. Click on the big blue button "Get Isntant Quote" or in the top right "Order Now"
3. In the top row labeled "Select Product", scroll to the right and select "Sheet Metal"
4. Now upload the .step models provided in the repo by dropping them into the according field.
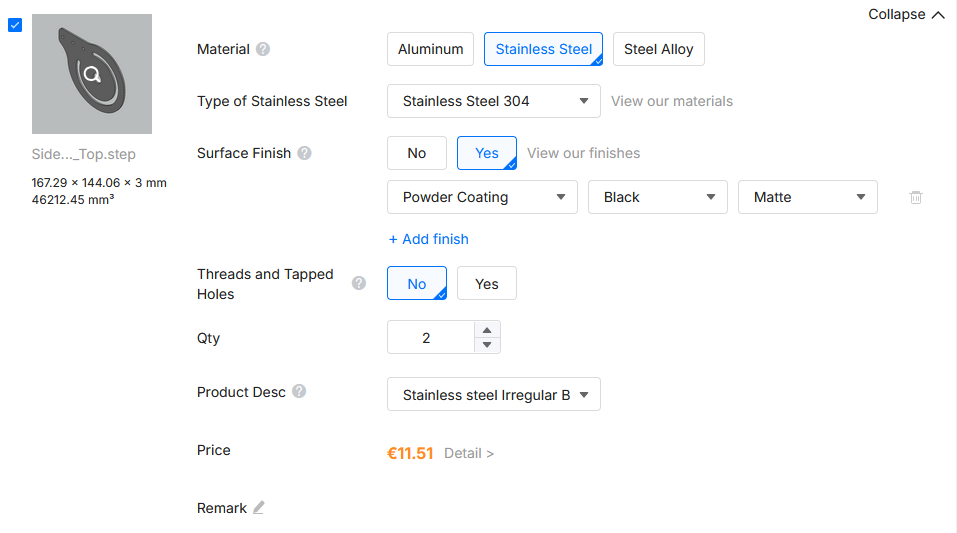
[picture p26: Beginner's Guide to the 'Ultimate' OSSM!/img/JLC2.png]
5. Select these settings: <br>
   You can choose any surface finish you like, or none at all, according to your preference!
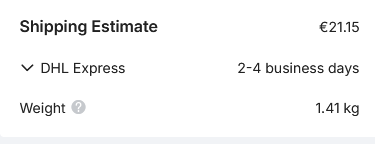
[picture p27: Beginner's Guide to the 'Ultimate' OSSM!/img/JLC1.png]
6. In the order summary on the right, look at the shipping. Open the shipping selection menu by clicking on the drop down arrow:<br> 
   Select the shipping according to your preferences. I usually go with EuroPacket, it's cheap.
7. Now press "Order"! Unfortunately you will need to create an account.
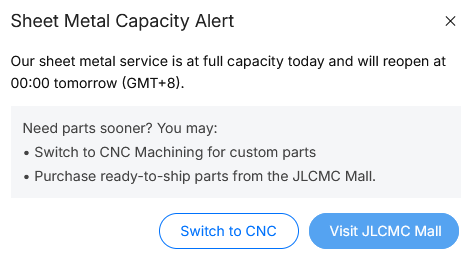
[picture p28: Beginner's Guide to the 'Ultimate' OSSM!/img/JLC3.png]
8. You may get a popup like this:<br> 
   Just come back at the stated time, in this case "tomorrow 00:00 GMT+8" and try to order again. Be on time for the best chances to get your order out. You may need a couple tries.
9. That's all! Enjoy!

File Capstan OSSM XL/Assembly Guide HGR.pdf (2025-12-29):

1. Bushing Pulley/Spindle/Drum/Capstan:
1. With the Bushing Pulley files printed, make sure the Bushing/Bearing Shell fits on top of the drum. Shouldn't be too loose or too tight. Top Part needs to fit on top as well with a somewhat secure fit. Also assure the pulley fits onto the motor shaft. Shouldn’t be too tight or loose. If things don't fit, adjust with the included .f3d file or pm me.
2. Take the bushing and slide the 24 mm shrink tubing on top. Cut it off so it fits well.
3. Heat the shrink tubing with a lighter or a heat gun. You can hold the bushing with some tongs or pliers, so you don’t burn yourself. Make sure to heat everywhere so it sticks to the bushing properly.
4. Spread some epoxy 2 part glue on the Bottom printed file.
5. Slide the Bushing/Bearing Shell on top. Put on the top part as well.
6. Put some weight on the Pulley and let it dry for 24h under pressure
7. Make sure the bushing holds well. It should be very rigid.

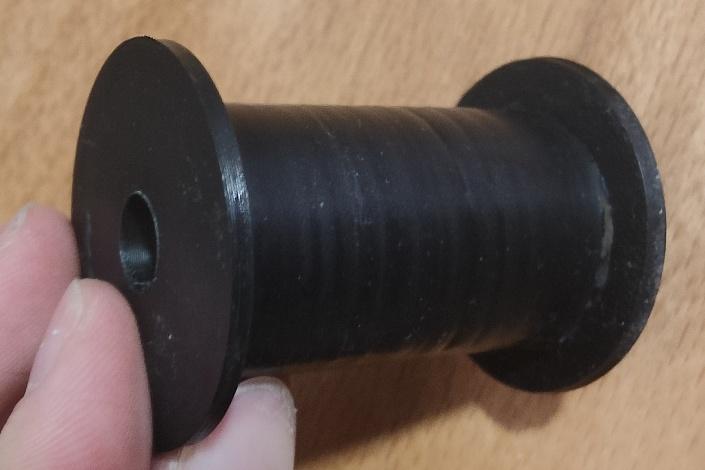
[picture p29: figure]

2. Clean the HGR20 Rail and HGH20HA Carriage (e.g. soaking in 99% isopropyl alcohol). Lube the carriage up well before mounting with some silicone grease

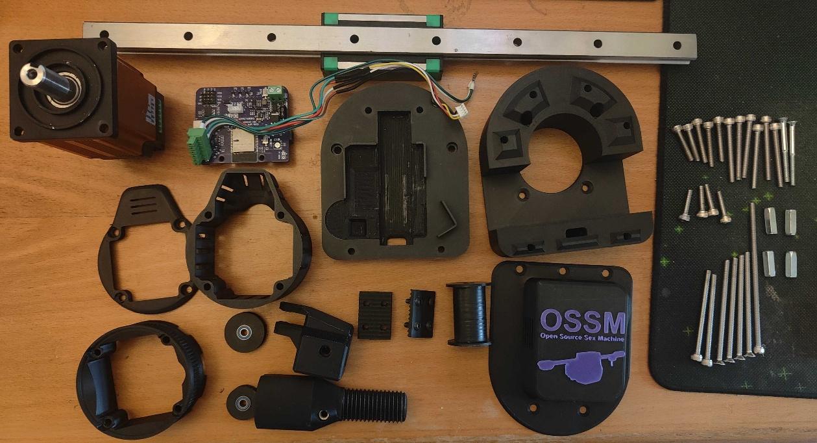
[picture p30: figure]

3. Mount the Motor Head Back to the Motor with Armpit’s 60AIM40F Ring behind (optional, if you want PitClamp Mounting) with 2 Hex Cap M5x65, 2 Countersunk M5x45 Screws and 4 M5 Nuts on the back. If you want to use the Motor Cover (https://github.com/SaladDressingHW/Salads-OSSM-Additions/tree/main/60AIM40F%20Motor%20Cover) replace the Nuts with M5x20 Coupling Nuts (as pictured). Make sure the Motor Terminal and the Notch in the Motor Ring are aligned to each other and the cable hole in the Motor Head Back right below the motor shaft. Ignore the cable in the second picture.

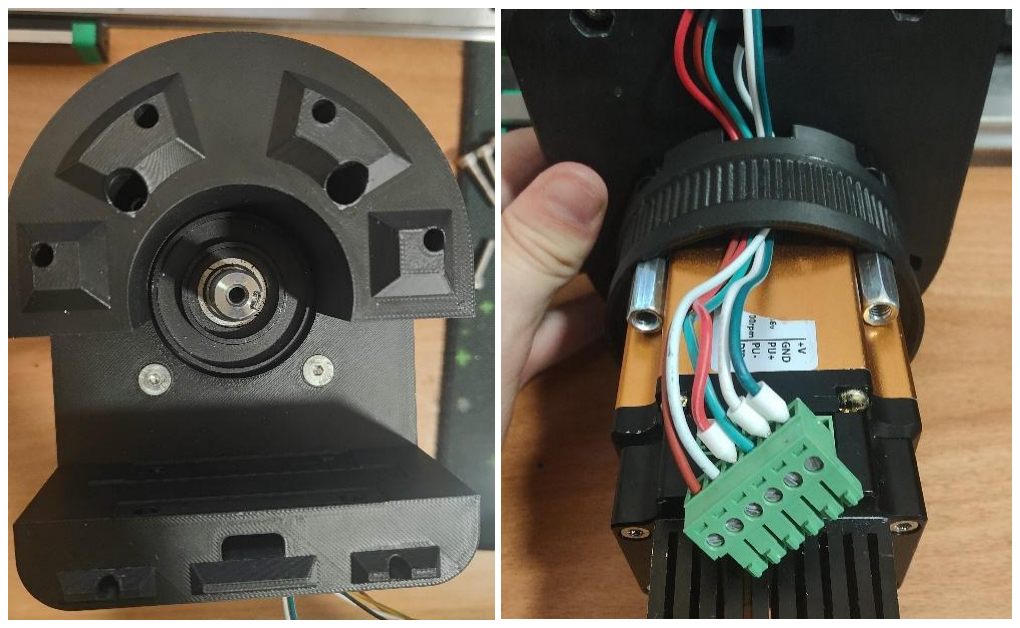
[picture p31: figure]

1. Screw the HGH20HA Rail Carriage to the Motor Head Back with 4 Hex Cap M5x20 screws. Slide the rail onto the carriage with the help of the plastic guide.

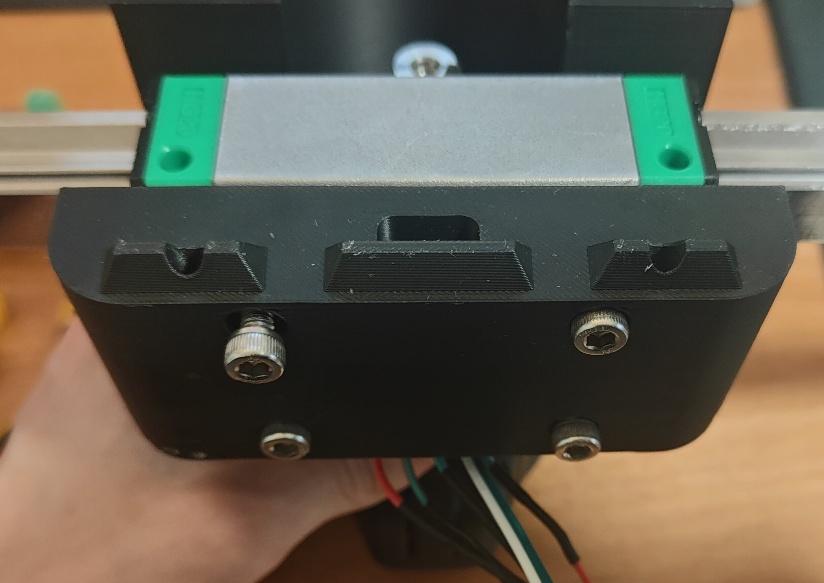
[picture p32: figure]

2. Slide the Rail End and End Effector onto the ends of the rail in the exact orientation shown below.

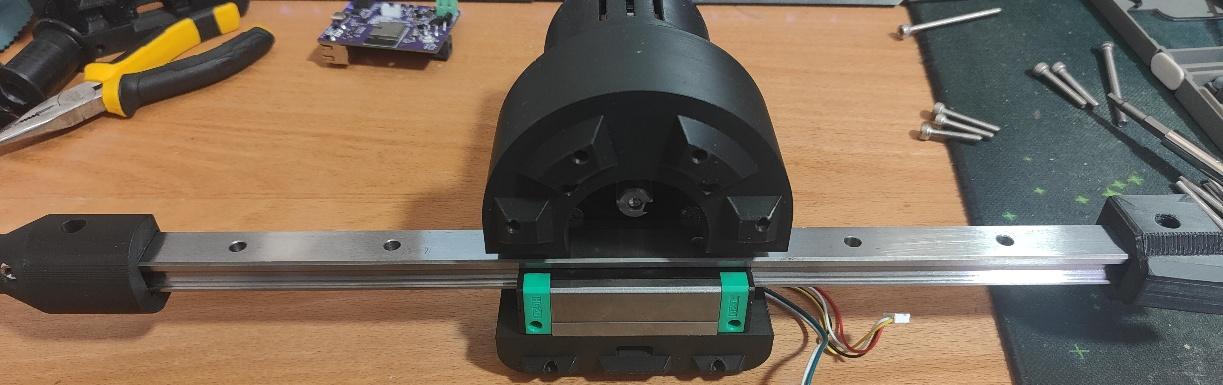
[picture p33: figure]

3. Fasten End Effector and Rail End each with a M5x30 Hex Cap Screw and a M5 Nut on the other side.
4. Insert 2 MR115 bearings each into big and small end pulleys. Mount the bigger pulley onto the Rail end with a M5x25 Hex Cap and the smaller one onto the End Effector with a M5x30 Hex Cap, as shown below. Use one M5 Nut each.

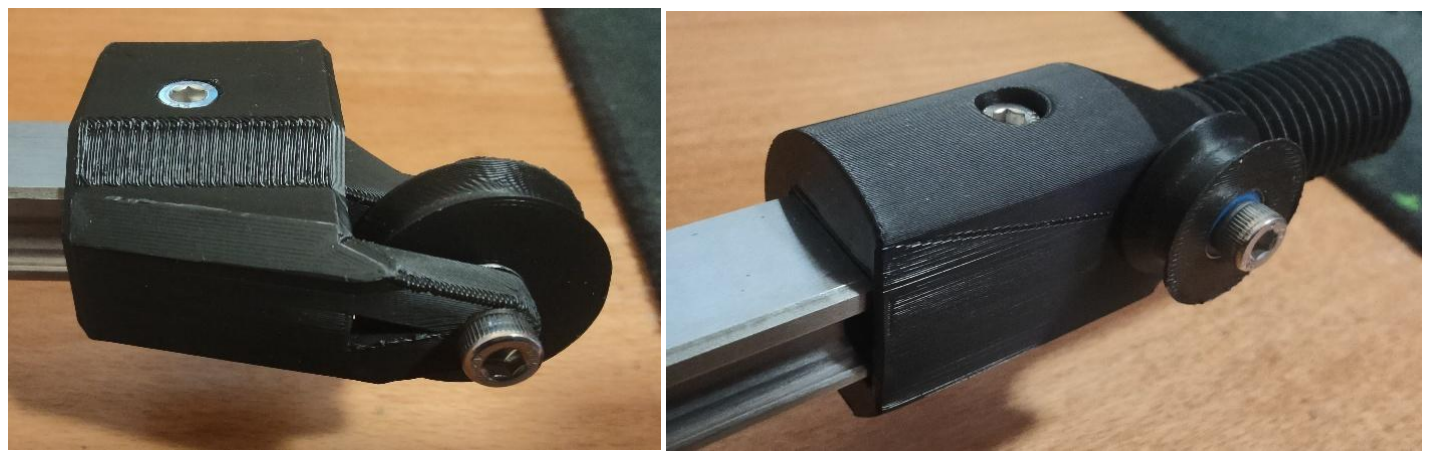
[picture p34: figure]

5. Slide the Capstan Drum onto the motor head.
6. Slide the motor head on the rail so it is roughly centered on the usable rail.
7. Take the rope and guide it through the circular hole on the side of the motor head through the “main channel” and out in the front (see pictures). Tie one end to a hole on the rail of your choosing. This makes the wrapping of the rope easier. Leave a generous length of rope on this end. Do not cut the rope.
8. Guide the rope around the End Effector’s Pulley from bottom to top.

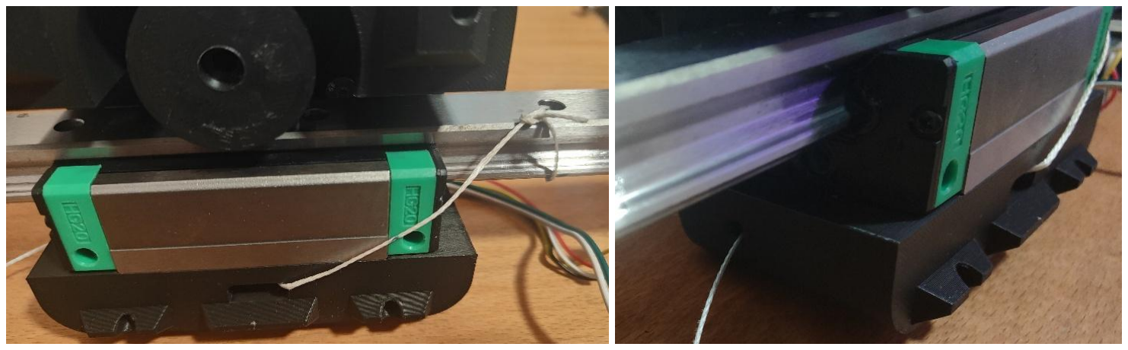
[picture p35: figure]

9. Wrap the rope rather tightly around the capstan pulley. The amount of wraps I used was 8, which works well with the Shrink Tubing I use. Your mileage may vary depending on how you increase the friction of the bushing. This is something you may need to play around with. More wraps have only the disadvantage of taking up more space, which makes it not possible to accommodate higher rail lengths. 8
wraps works well with 450mm rail length. Not
enough wraps will result in slipping of the rope.

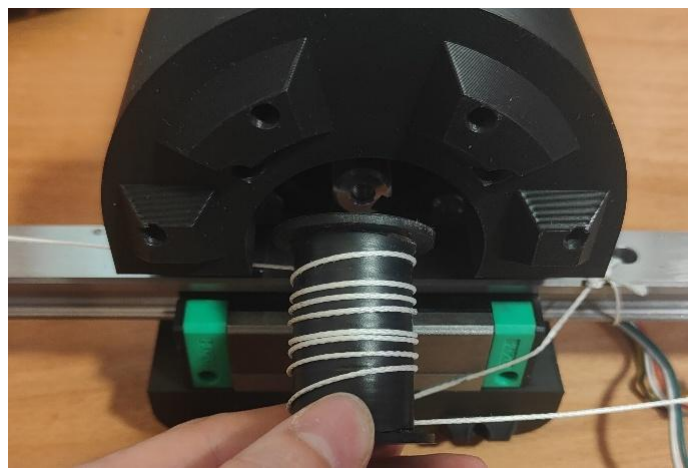
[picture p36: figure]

The more wraps, the harder it is for the rope to slip. When you are done, roughly center the wraps on the drum by sliding them around.
10. Guide the rope as pictured below and slide the end through the circular hole on the left side of the motor head, again through the “main channel” and out through the front (see pictures).

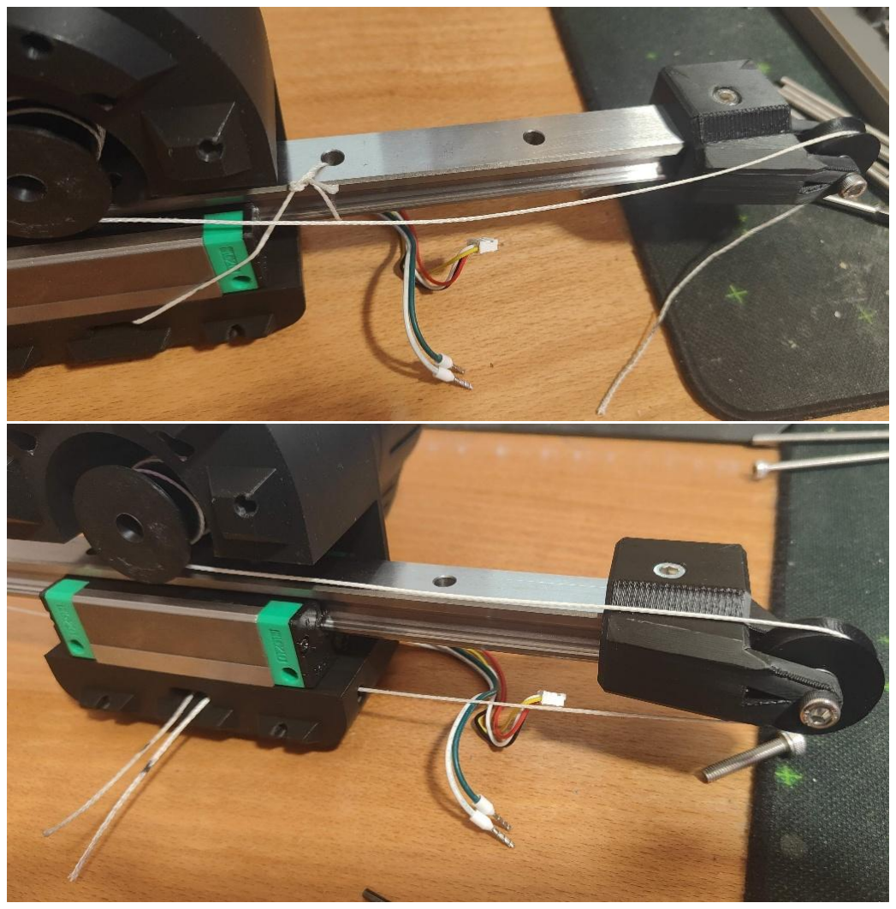
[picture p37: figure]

11. You can let go of the rope. This will relieve some tension from the wraps, but that is no problem, we can tension it as much as we like later.
12. Push the pulley onto the motor shaft completely. Screw it onto the shaft using a M5x25 Hex Cap screw. You don’t need to screw it very tight.

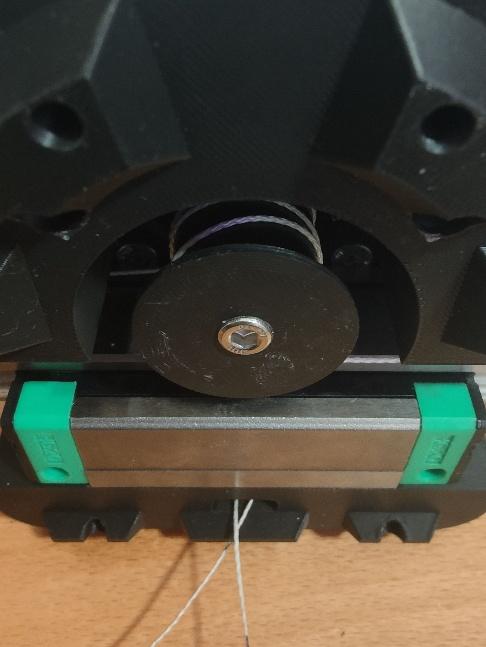
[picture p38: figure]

13. Take the Motor Head Front part. Push in the standoffs in the fitting slots. Use violence if needed. Make sure it fits properly and take out the bottom one as that obstructs the next steps.
14. Push 4 M4 and 1 M5 Nuts into the lower part of the tensioner.
15. Insert the lower part of the tensioner into the Motor Head front part as pictured below.
16. Push the Tensioner around a bit to make sure it moves around.
17. Put the Motor Head Front onto the Motor Head Back with 2 M5x65 Hex Cap Screws and slide the rope through the appropriate passthrough hole.

18. Flip the rope ends up, onto the Tensioner and tension them by pulling them. Now put the top part of the Tensioner on top and screw it tight with 4x M4x12 ISO7380 screws. Ignore the cables in the picture.

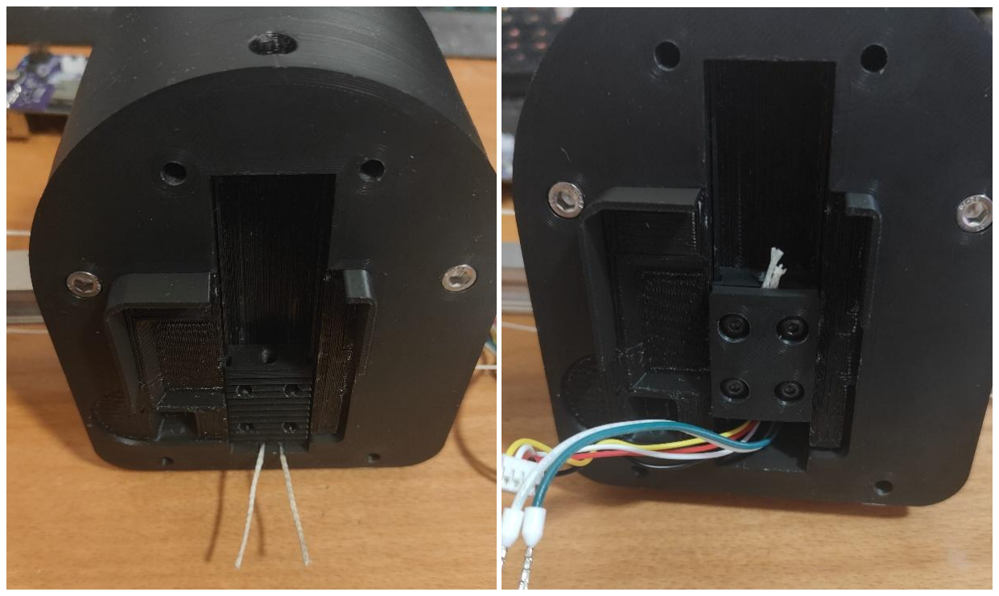
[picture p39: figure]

19. Take the 300mm JST Header cable as well as some awg 18 or thicker (not too thick) 2 pin cable (power cable). Don’t cut anything off
20. Crimp one end of the power cable.
21. Route the power and JST cable through the main channel and Motor ring to the Motor. Screw the crimped end of the power cable and the cable end of the JST cable into the motor terminal. Check the labels on motor and control board pcb. They need to match.

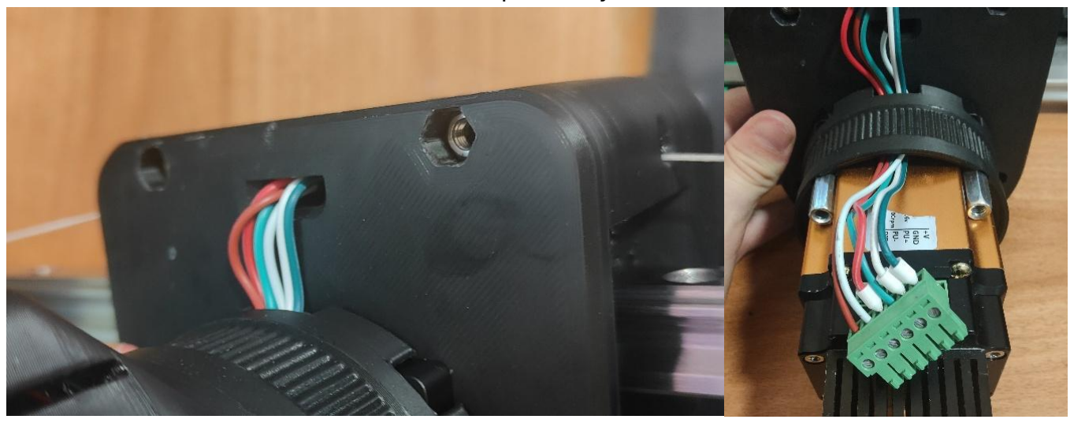
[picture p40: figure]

22. Check Cable lengths. Look at a picture further down how the PCB is mounted. There needs to be enough cable to mount it without tension. Avoid having too high lengths of cable though. Cut it shorter if needed.
23. Crimp the other ends of the cable.
24. Connect JST Header and Power cable to the control board.
25. Screw an M5x110 Hex Cap screw from the top of the Motor Head Front through the Tensioner. Turning this screw will slide the Tensioner up and therefore tighten the rope. Tighten it a bit for now.
26. Clip on the lowest standoff back onto the Motor Head Front.

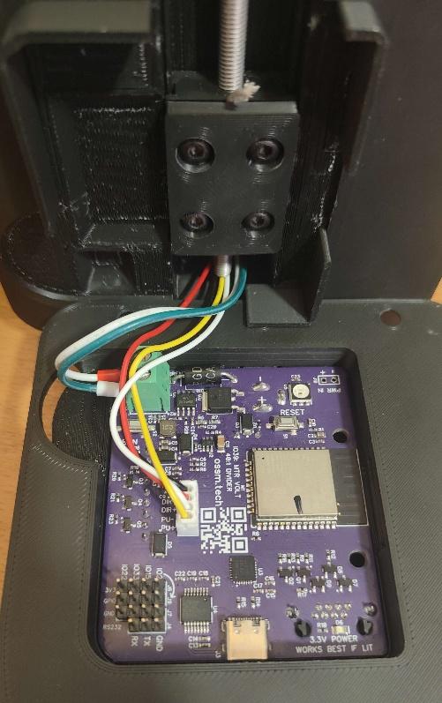
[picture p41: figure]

27. Now turn the M5x110 screw to tension the rope. Tension it guitar string tight. Move around the rail a bit and see if anything is wrong. The motion should be very fluent. Make sure the rope wraps are roughly centered on the capstan pulley. If they are not, it may be that it gets hard to push the rail to the end because the rope wraps over itself (thus increasing diameter of the capstan pulley -> longer rope needed). If you have issues with this and can’t get it to work, feel free to pm on discord.
28. The rope will stretch a tiny bit over the first few hours of use. Retension accordingly to keep it guitar string tight or even tighter. The tighter the rope is tensioned, the less shifting on the rope on the drum you will have (in extreme conditions). I haven’t played around with limits on how tight is too tight, but at some point the tensioner will probably fail. Before use, always make sure the rope is properly tensioned.
29. Cut the rope now but leave some redundancy in length.
30. Finally, screw down the front cover with 4x M5x75 countersunk screws and 4x M5 Nuts on the back.

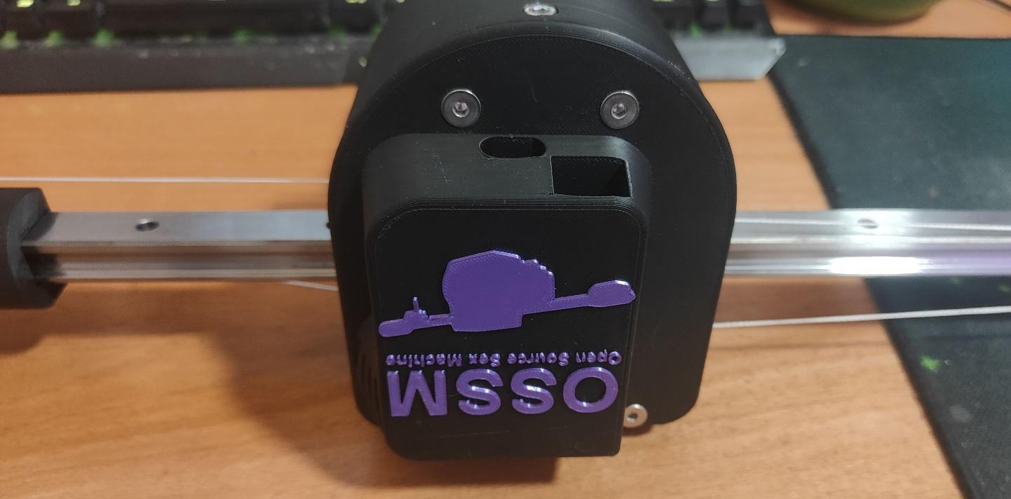
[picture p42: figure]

31. Have fun!

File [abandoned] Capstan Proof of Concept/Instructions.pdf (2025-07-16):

1. Insert 2 M3 Nuts into the back of the Main Part of the End Effector. Make sure they are properly seated, e.g. by screwing the min from the other side

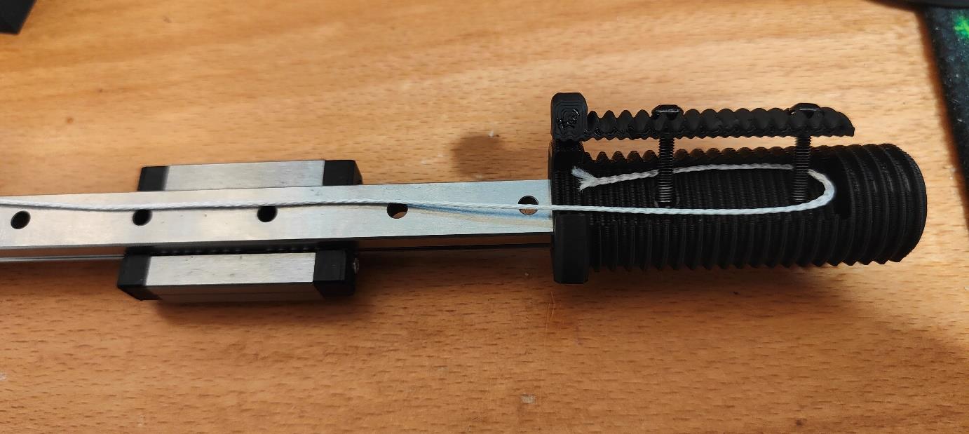
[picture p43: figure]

2. Slide the End Effector onto the rail in the shown orientation. Lay the rope into the teethed channel in a U-Shape.DO NOT CUT THE ROPE YET. Insert 2 M3x16 ISO7380 Screws into the Top Part of the End Effector and screw it on hand tight. Be careful not to destroy your screw heads.

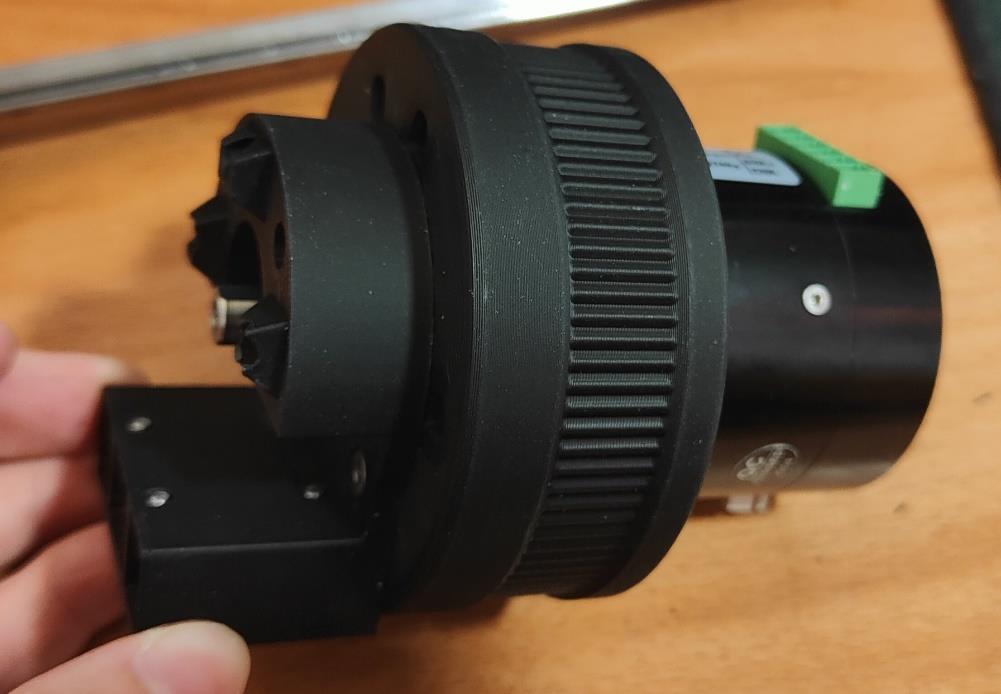
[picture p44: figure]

3. Insert 5 M5 Nuts into the Back of the back of the Motor Head. Again, make sure they are seated properly. Screw the Back Part of the Motor Head through the PitClamp Ring into the Motor with 2 M3x12 Countersunk and 2 M3x12 Hex Cap Screws.

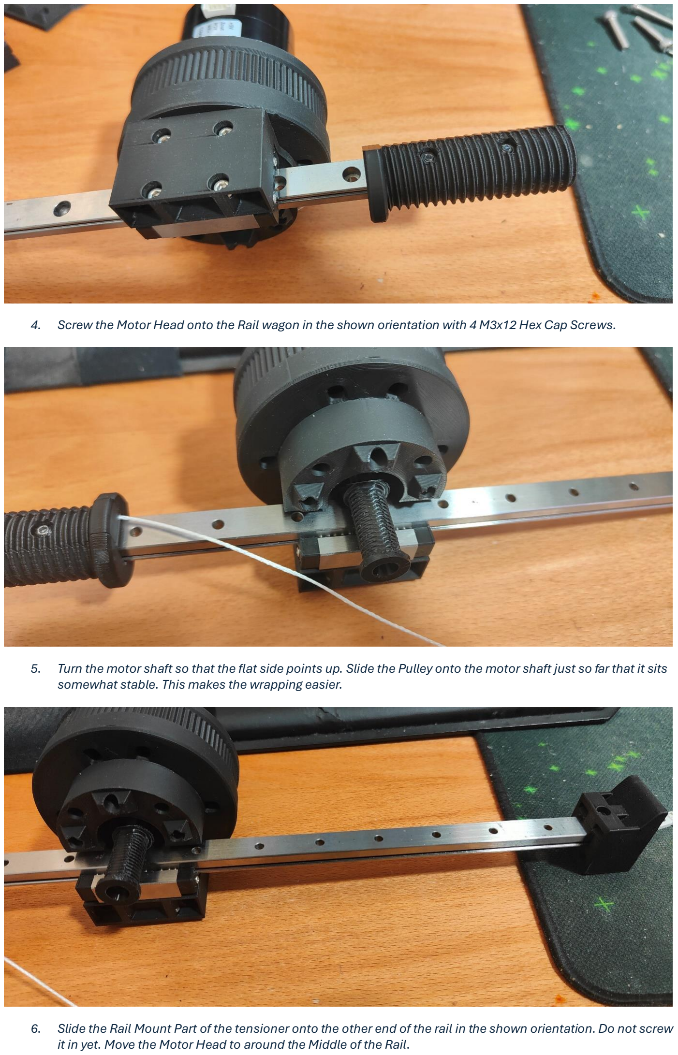
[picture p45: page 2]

4. Screw the Motor Head onto the Rail wagon in the shown orientation with 4 M3x12 Hex Cap Screws.
5. Turn the motor shaft so that the flat side points up. Slide the Pulley onto the motor shaft just so far that it sits somewhat stable. This makes the wrapping easier.
6. Slide the Rail Mount Part of the tensioner onto the other end of the rail in the shown orientation. Do not screw it in yet. Move the Motor Head to around the Middle of the Rail.

7. Wrap the rope around the Pulley. Loop from underneath the pulley upwards, counterclockwise. Wrap it around 5 times so that the 5 wraps are in the middle as best as possible. See picture. Keep the rope tensioned while wrapping.

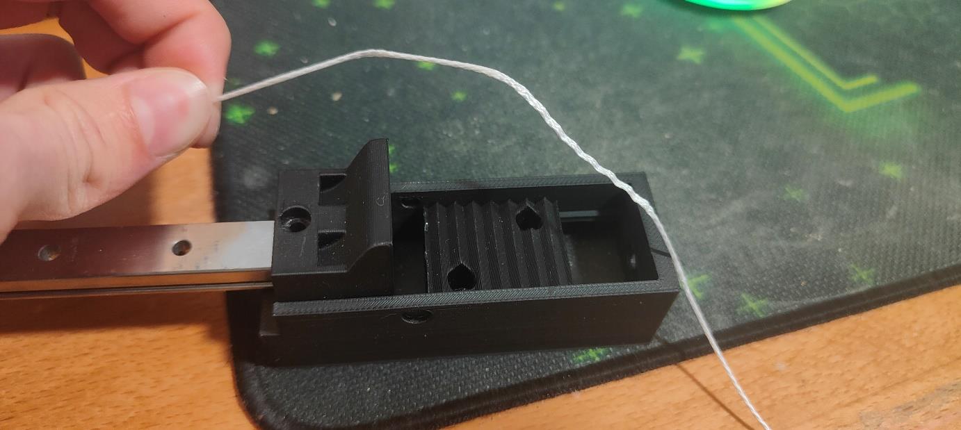
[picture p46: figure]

8. Place a M3 Nut into the Underside of the Slider Part of the tensioner as well as in the side. Place 2 M5 Nuts into the underside and another one into the side of the lower part of the rope clamp. Also place 2 M5 Nuts into the back of the Rail Mount. Slide the Lower Part of the rope clamp into the slider and place the slider underneath the Rail Mount like shown above.

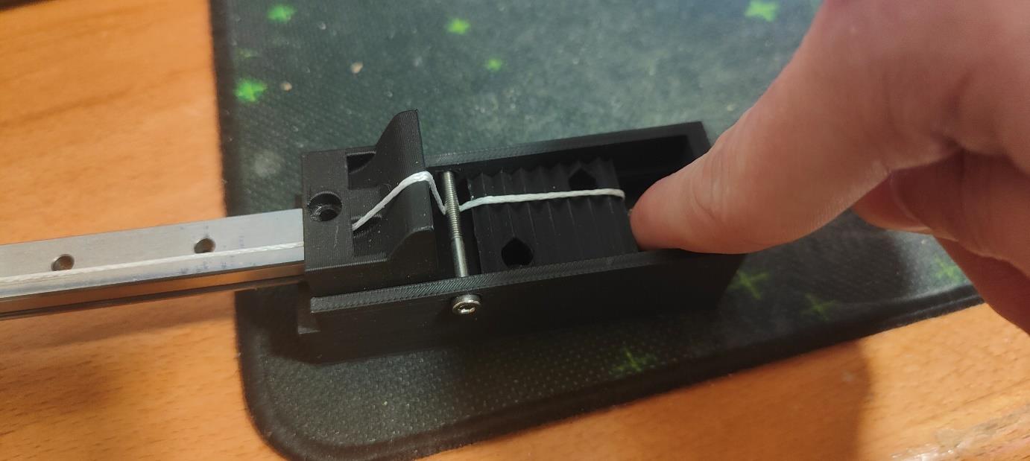
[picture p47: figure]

9. Guide the rope through the right hole, over the slope and down. Screw in a M3x30 Screw slightly like shown. Tension the rope over the Teeth of the clamp.

10. Screw in the upper part of the rope clamp on top of the lower part with 2 M5x25 screws. Make it tight. Screw another 2 M5x25 screws through the front of the Slider through the rail Mount into the nuts at the back. Screw in the Rail Mount with a M3x30 Screw. Finally, Put the M5x50 Bolt through the back of the Tensioner through the lower part of the rope clamp. To Tension, just tighten the screw. With the Motor Head in the middle of the rail, tension the rope but not too much.
11. Last but not least, fully insert the Pulley and screw it in with a M4x16 Screw. Not too tight here as well. You will need a plier to hold the pulley in place. Screw the front part of the Motor Head on top with 5 M5x35 Countersunk screws.
12. You will need to play around with it a bit to see if everything works, and retention should the rope stretch a bit.

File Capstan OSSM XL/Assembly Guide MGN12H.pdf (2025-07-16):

1. Bushing Pulley/Spindle/Drum/Capstan:
1. With the Bushing Pulley files printed, make sure the Bushing/Bearing Shell fits on top of the drum. Shouldn't be too loose or too tight. Top Part needs to fit on top as well with a somewhat secure fit. Also assure the pulley fits onto the motor shaft. Shouldn’t be too tight or loose. If things don't fit, adjust with the included .f3d file or pm me.
2. Spread some epoxy 2 part glue on the printed file.
3. Slide the Bushing/Bearing Shell on top. Put on the top part as well.
4. Put some weight on the Pulley and let it dry for 24h under pressure
5. Make sure the bushing holds well. It should be very rigid.
6. Wrap some grippy tape around the pulley. I used kinesio tape, which works quite well

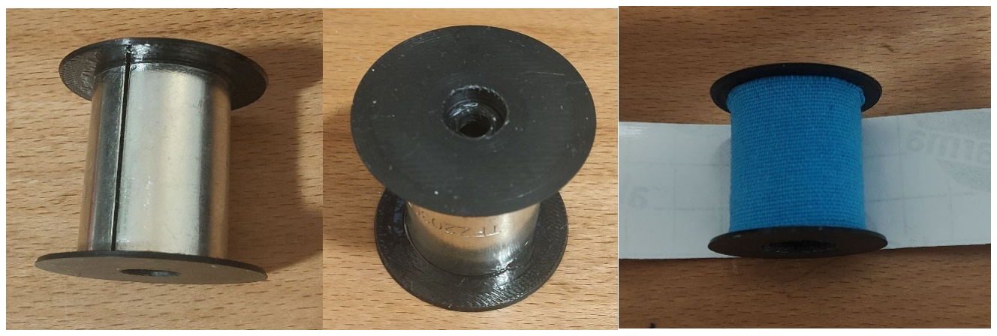
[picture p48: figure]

2. Clean the MGN12H Rail and Wagon (e.g. soaking in 99% isopropyl alcohol)
3. Screw the MGN12H Rail wagon to the Motor Head Back with 4 HexCap M3x12 screws
4. Mount the Motor Head Back to the Motor with Armpit’s 60AIM40F Ring behind (optional, if you want PitClamp Mounting) with 2 Hex Cap M5x45, 2 Countersunk M5x45 Screws and 4 M5 Nuts on the back. Make sure the Motor Terminal and the Notch in the Motor Ring are aligned to each other and the cable hole in the Motor Head Back right below the motor shaft.

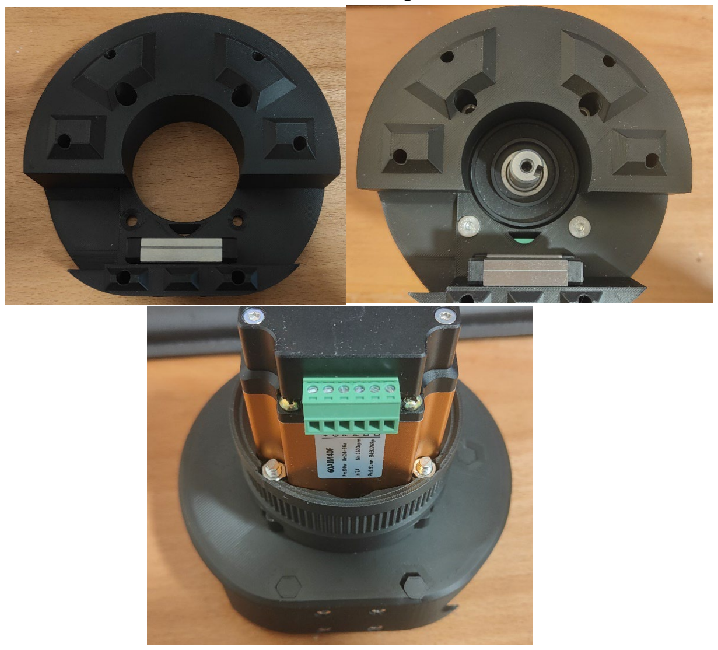
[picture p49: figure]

5. Insert 2 MR115 bearings into the 8mm end pulley, 3 MR115 bearings into the 12mm end pulley.
6. Secure the 8mm Pulley to the end effector and the 12mm end pulley to the rail end with a ISO 7380 M5x20 screw each.
7. Slide End Effector and Rail End onto the rail as pictured below. Secure the End Effector with 2x M3x16 Hex Cap Screws and the Rail End with 1x M3x12 Hex Cap Screw

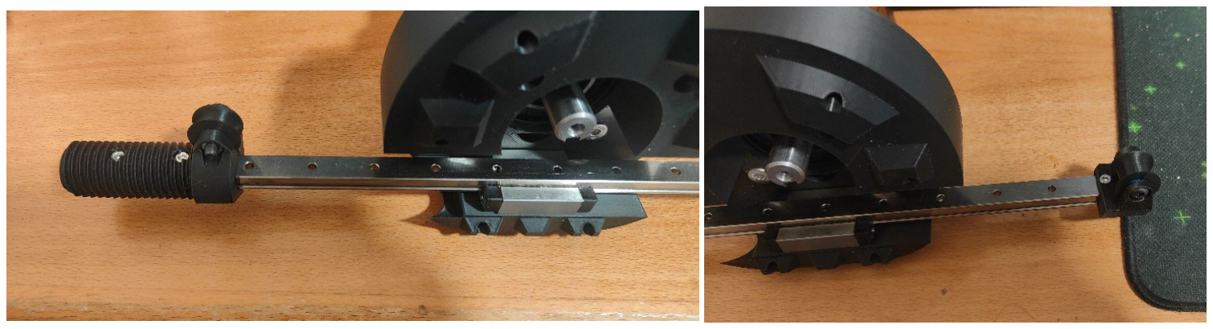
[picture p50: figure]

8. Channel the jst and 2 pin cable through the central hole below the motor shaft on the Motor Head Back
9. Slide the Pulley onto the motor head. Do not slide it on completely, just push it on enough for it to have a somewhat stable fit. This will make the wrapping of the rope easier.
10. Slide the motor head on the rail so it is roughly centered to the usable rail.
11. Take the rope and tie one end to a hole on the rail of your choosing. This makes the wrapping of the rope easier. Leave a generous length of rope on this end. Do not cut the rope.
12. Guide the rope around the end pulleys and the capstan like pictured below.

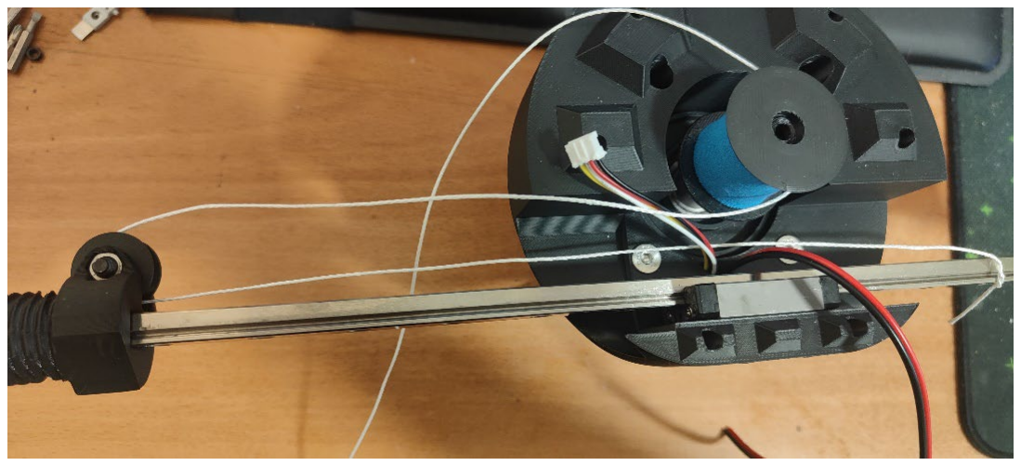
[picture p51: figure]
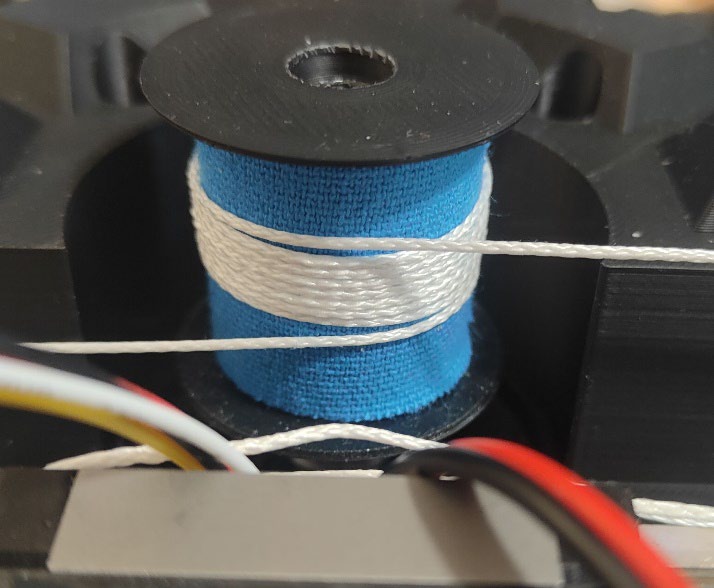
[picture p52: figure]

13. Wrap the rope rather tightly around the capstan pulley. Try to keep the wraps on the drum roughly centered. The amount of wraps I used was 8, which works well with the Kinesio tape I used. Your mileage may vary depending on which tape you used. This is something you may need to play around with. More wraps have only the disadvantage of taking up more space, which makes it not possible to accommodate higher rail lengths. 8 wraps works well with 450mm rail length. Not enough wraps will result in slipping of the rope. The more wraps, the harder it is for the rope to slip.

14. If you use the 3d printed Pulley with the integrated grooves (not the bushing pulley), same applies here, though you will need less wraps. 5 was enough if I remember correctly.
15. Guide the rope as pictured below

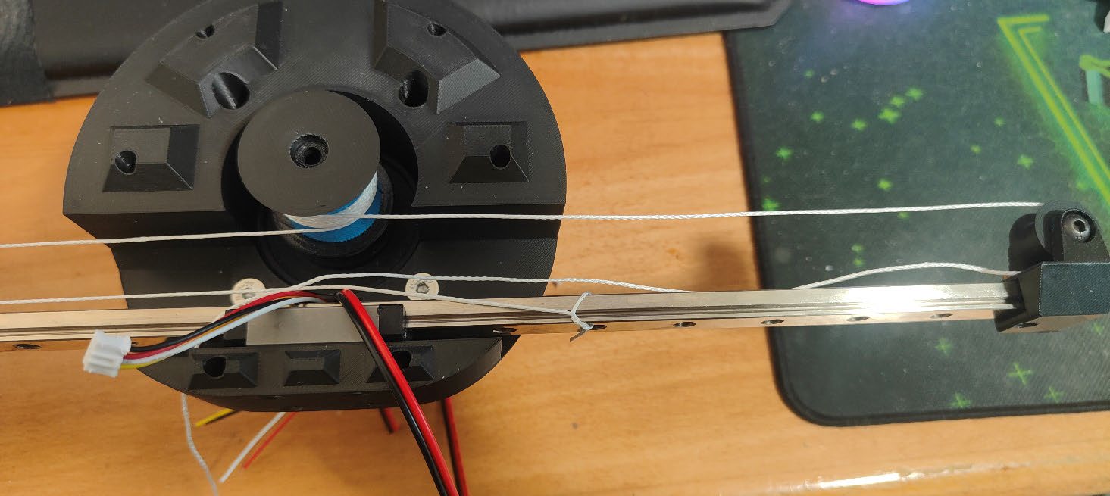
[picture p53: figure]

16. You can let go of the rope. This will relieve some tension from the wraps, but that is no problem, we can tension it as much as we like later.
17. Push the pulley onto the motor shaft completely. Screw it onto the shaft using a ISO 7380 M5x12 screw. You don’t need to screw it very tight.
18. Take the Motor Head Front part. Push in the standoffs in the fitting slots. Use violence if needed.
19. Push 4 M4 and 1 M5 Nuts into the lower part of the tensioner.
20. Insert the lower part of the tensioner into the Motor Head front part as pictured below. Insert the M5x80 screw from the appropriate hole on top and screw it into the lower tensioner part.

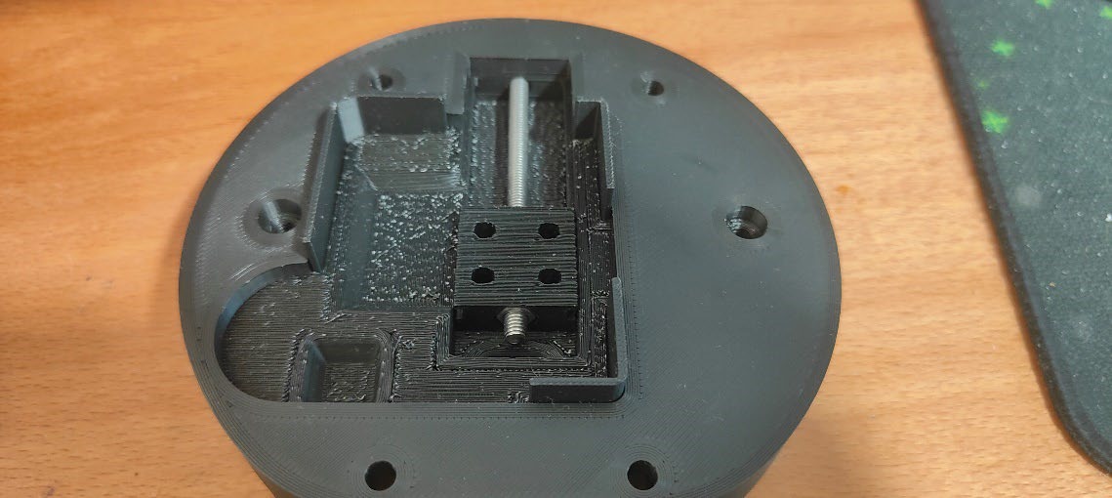
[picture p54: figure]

21. Push the Tensioner around a bit to make sure it moves around.
22. Put the Motor Head Front onto the Motor Head Back. For this, first guide the jst and 2 pin cables through the hole just below the tensioner. Then untie the rope end and guide both rope ends through the same hole.

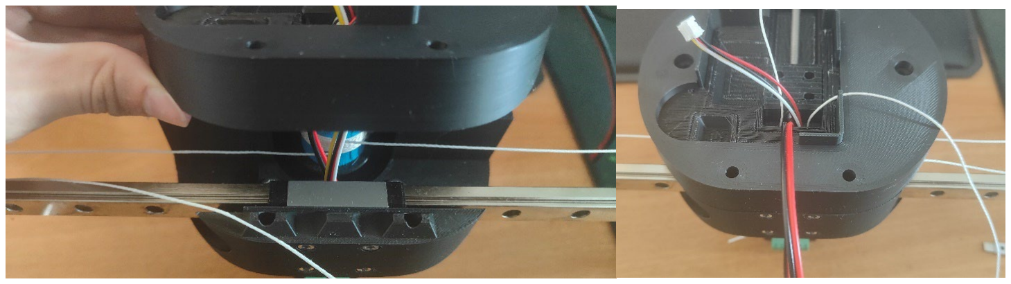
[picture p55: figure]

23. Insert 4 ISO 7380 M4x12 screws into the tensioner top part.
24. Tension the rope ends and pull them over the teeth of the tensioner.
25. Place the tensioner top part onto the lower part and screw it tight. You can make it quite tight.

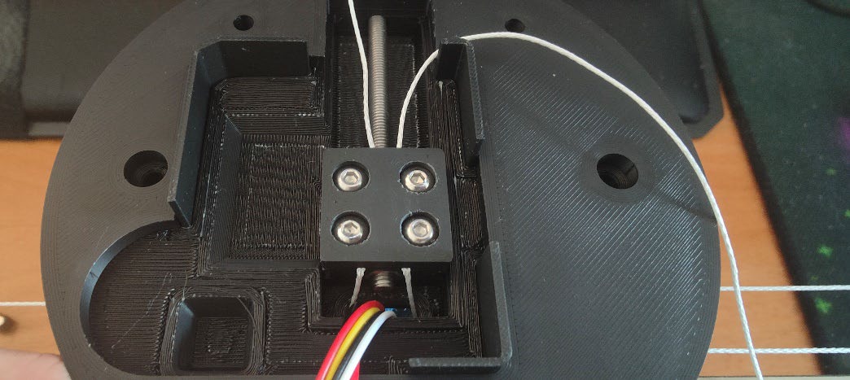
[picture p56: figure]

26. Make sure the rope goes over the little blocks on the underside of the Motor Head Front, as pictured below

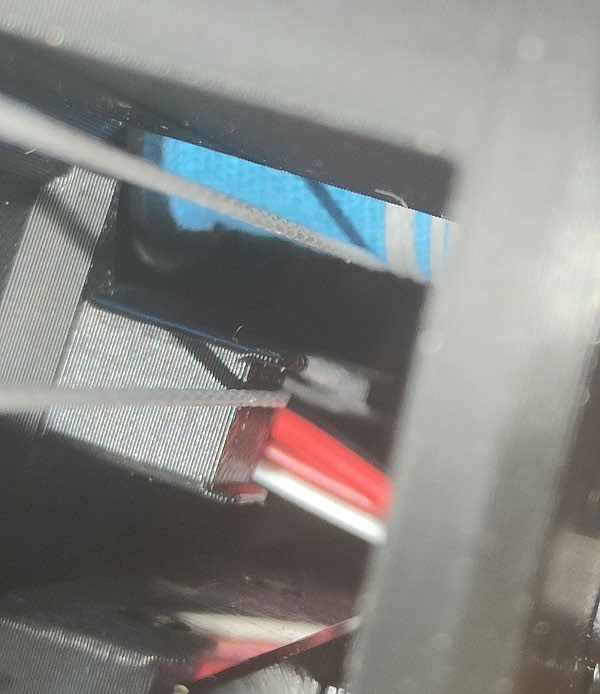
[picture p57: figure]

27. Mount the Top with 2 M5x45 Hex Cap screws and 2 M5 Nuts on the back
28. Now turn the M5x80 screw to tension the rope. Tension it guitar string tight. Move around the rail a bit and see if anything is wrong. The motion should be very fluent. Make sure the rope wraps are roughly centered on the capstan pulley. If they are not, it may be that it gets hard to push the rail to the end because the rope wraps over itself (thus increasing diameter of the capstan pulley -> longer rope needed). If you have issues with this and can’t get it to work, feel free to write on discord.

29. Hold the rope ends tightly, screw of the tensioner top part, and reset the position of the tensioner back down again. Then screw in the tensioner top part again. This is done so you have some redundancy in retensioning.
30. The rope will stretch a tiny bit over the first few hours of use. Retension accordingly to keep it guitar string tight or even tighter. The tighter the rope is tensioned, the less shifting on the rope on the drum you will have (in extreme conditions). However, too tight of a tension may damage the tape on the capstan pulley over time. Before use, always make sure the rope is properly tensioned.
31. Cut the rope now but leave some redundancy in length.
32. Crimp the cable ends with terminal crimps.
33. Plug the JST cable into the header on the ossm control board and screw in the cable ends into the terminal block
34. Place the ossm control board onto the standoffs with the side with the esp chip facing down.
35. Cut the cables to length and screw the other side into the motors terminal.
36. Finally, screw down the front cover with 4x M5x45 countersunk screws and 4x M5 Nuts on the back.

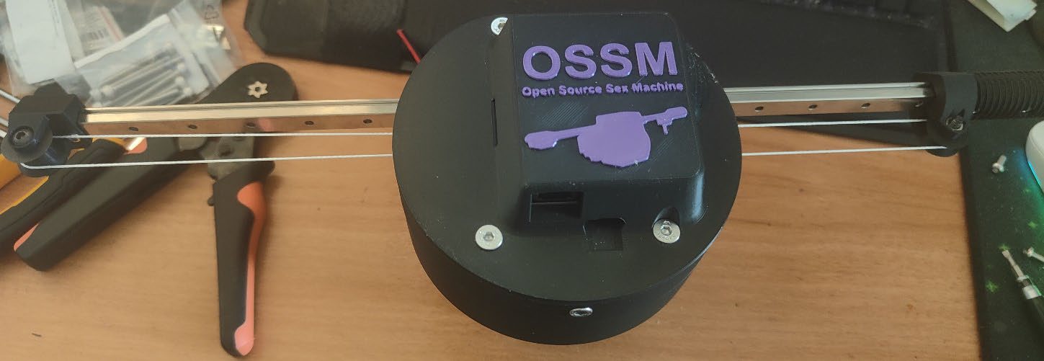
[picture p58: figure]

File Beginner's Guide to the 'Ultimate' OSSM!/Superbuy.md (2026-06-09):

This is a short guide on how to oder on Superbuy! E.g. for odering the 60AIM40F Motor.
### What is Superbuy?
Do not be alarmed by it's sketchy looks! Superbuy is not a shop! Superbuy is a chinese forward shipping service. This means they will order a local product for you, inspect it and then send it to you. There are also quite a few services you can order with that as well, if you want them. That means you can buy at places like taobao relatively hassle free, and get local support on the actual items, before they get shipped to you. Roughly, the general process goes like this:
1. Order a product
2. Inspect wether everythign is fine or not. Send products back or let them get replaced accordingly.
3. Get the product shipped to you.

### Example
On the example of the 60AIM40F, let me show you the detailed steps!
1. You will need a Superbuy account to order. Register or log in!
2. Open the product you want to order, either by placing the link from the original shop (e.g. Taobao) into the  product Bar right at the top, or by opening a link, such as the one to the [60AIM40F](https://www.superbuy.com/en/page/buy/?url=https://item.taobao.com/item.htm?id=668578585661).
3. Select the options you want and add the product to cart.
4. Repeat with any other items you might want.
5. Go to your cart and select the products you want to order by checking the box on the left of them. Click "Submit"
6. On the next screen things might get a little unknown. Start by selecting the country the item will ultimately be shipped to, so where you live, at hte top. Then it is time to select inspection and service options. All of them are optional, and I rarely use them. I jsut leave everything as is usually.
7. When you are done slecting options, again, press "Submit".
8. Complete payment. Once payment is processed, the product will now get ordered by superbuy staff for you. You can check the orders status in your orders tab. You can find that by clicking on your profile, then on the left, select "My Orders".
9. Sometimes, prices change between the time you place the order and the superbuy staff orders the product. In that case, you will either have to pay the additional cost when you get notified or cancel the order.
10. Once your product is there, you can inspect it. To do that, open the pictures linked in your orders tab. If everything looks fine, you can continue. You can also order soem additional services liek extra photos with instructions if you are not sure. If you find a defect, you can send the item back or get a replacement.
11. If everything is fine, on the left, go to the "My warehouse" tab. here you can see all of your items ready for shipping. Select the ones you want to ship, and continue.
12. You cna either select the expert shipping service, where someone will try to find a good cheap shipping option for you, or you can do it yourself. I myself have always done it myself and can't speak on the quality of the exoert shipping service.
13. Shipping price is calculated by weight and measurements of the product. To see the details of the automatically calculated price, hover over "Detail"
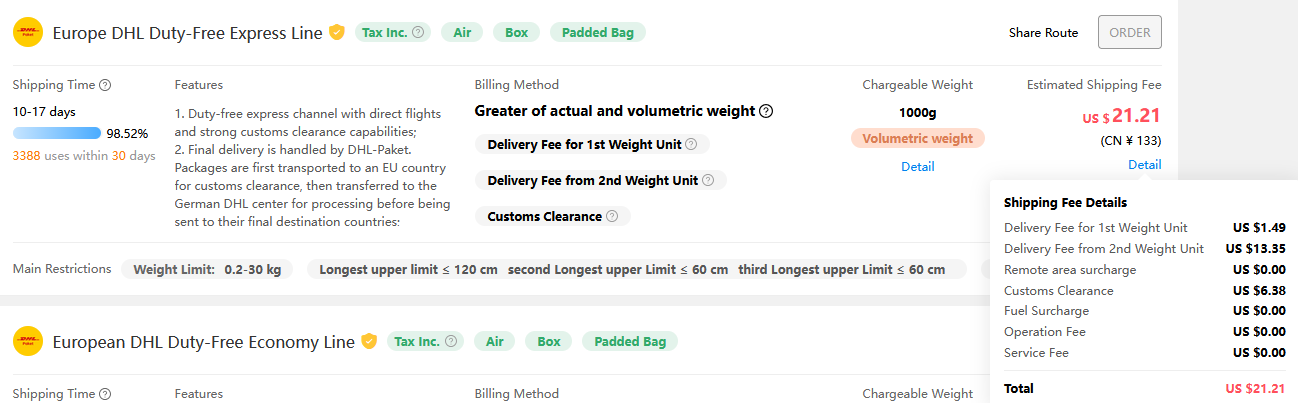
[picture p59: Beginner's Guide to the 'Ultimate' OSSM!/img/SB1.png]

You can also hover over the question marks in the middle to see more info on how the price is calculated relative to weight and measurements.
Another important thing is of course the shipping time. Superbuy has a confirmation button for when you have received your item. With that, it keeps a statistic on shipping time for each service. You can see that statistic by hovering over the days number, in the screenshot below "10-17 days":
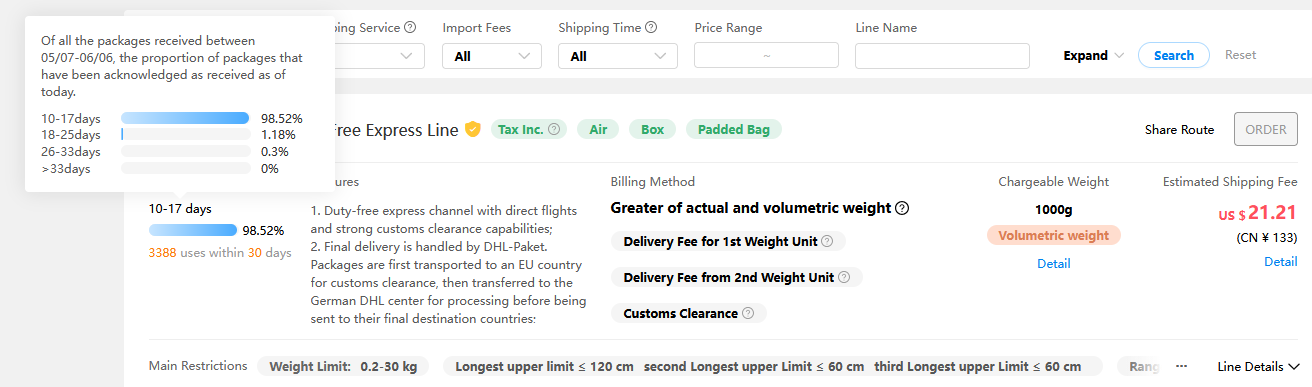
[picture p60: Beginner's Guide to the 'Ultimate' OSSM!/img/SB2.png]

This is a neat tool to see when you are likely to get your package!
I usually select one of the cheaper or the cheapest option. So far I have shipped with Yun Express, EUB, and EMS. All work great, though I have like Yun Express the most so far. They have been the quickest.
14. After you have selected your shipping service, you will now have to declare the tax value. Just put in the value you paid for the product when ordering from superbuy. You **can** theoretically put in any value you want, but I am not goingto elaborate on the risks of doing that (Tax fraud).
15. Finish up by confirming the parcel order! You can review the parcels status by going to the "My parcels" tab in your profile.
16. Happy shopping!

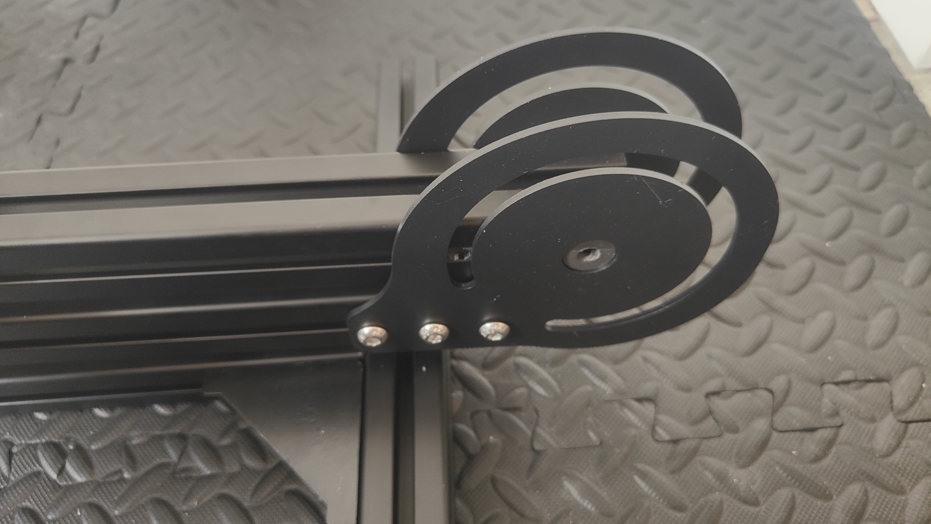
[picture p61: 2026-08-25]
Shicks Mount Modernised/Assembly Guide (WIP)/img/IMG20260821130546.jpg

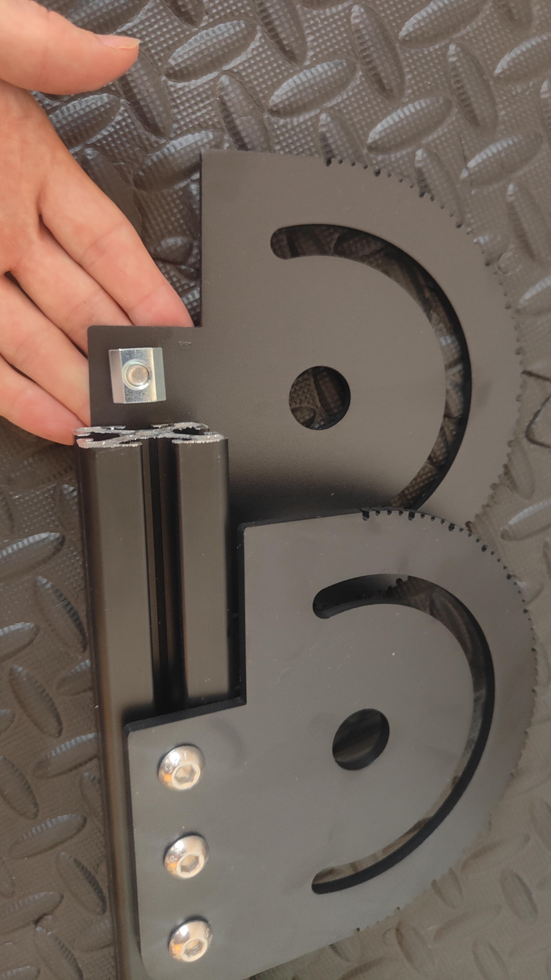
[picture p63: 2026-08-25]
Shicks Mount Modernised/Assembly Guide (WIP)/img/IMG20260820184301.jpg

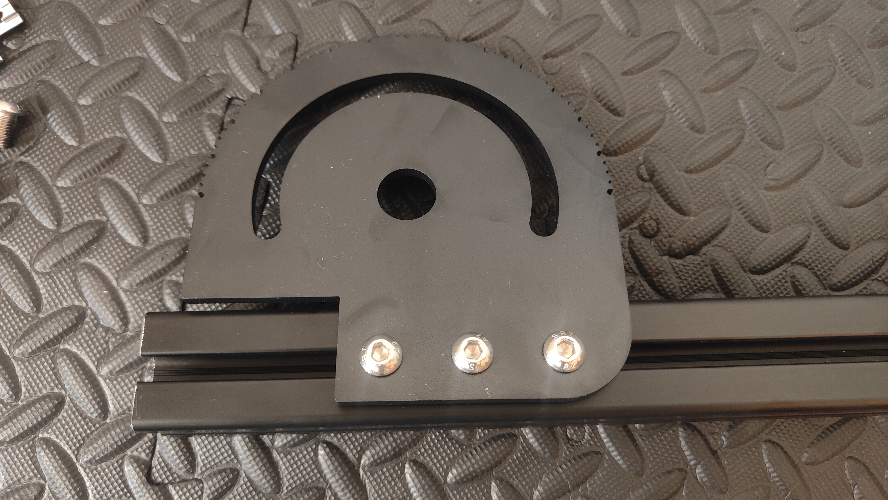
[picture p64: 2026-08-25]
Shicks Mount Modernised/Assembly Guide (WIP)/img/IMG20260820183850.jpg

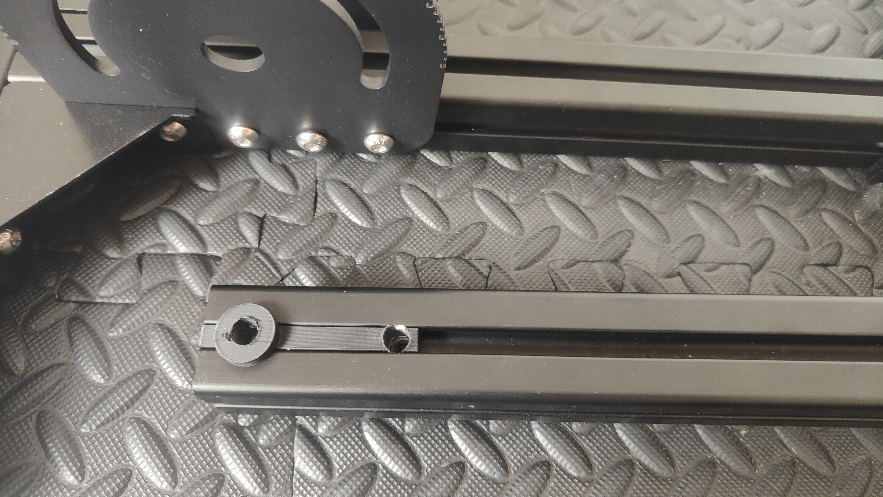
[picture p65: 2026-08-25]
Shicks Mount Modernised/Assembly Guide (WIP)/img/IMG20260821125007.jpg

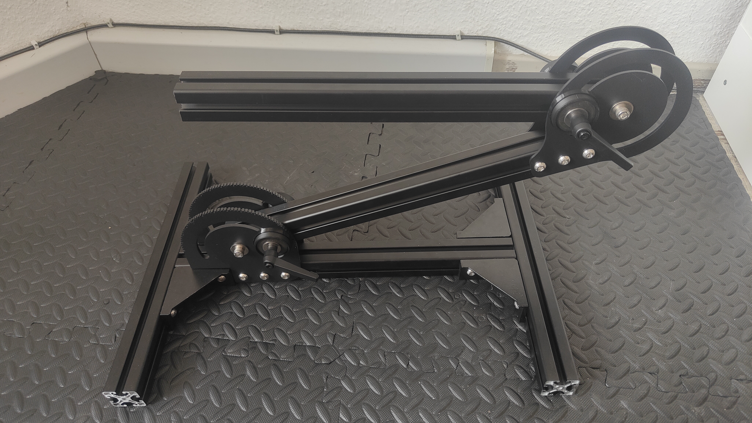
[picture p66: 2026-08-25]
Shicks Mount Modernised/Assembly Guide (WIP)/img/IMG20260821131130.jpg

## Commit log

2025-07-16 initial release
    [12mmEndPulley.3mf, 12mmEndPulley.stl, 8mmEndPulley.3mf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]
2025-07-20 decreased rail wagon clamp tolerance
    [MotorHead_FrontAIO.stl]
2025-08-08 added olympic version
    [Weight Plate Bracket Olympic.step]
2025-09-18 rounded front
    [strap12segments.stl, tpuStrap.f3d, universal_strap_3mm_notch.stl]
2026-05-06 20mm hole spacing from rail end
    [EndEffector_20mm.stl, RailEnd_20mm.stl]
2026-06-09 beta release
    [HingeAluxprofile.f3z, HingeLong_Bottom.stl, HingeLong_Bottom_Aluxprofile.stl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]
